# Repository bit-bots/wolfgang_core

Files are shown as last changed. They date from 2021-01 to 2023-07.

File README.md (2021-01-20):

# Wolfgang CORE
COntrolling and REgulating electronics for the Wolfgang robot platform

Documentation can be found [here](http://doku.bit-bots.de/meta/manual/hardware/electronics/wolfgang_core.html).

## Features
* Power over Ethernet (PoE) power source (for ethernet camera)
* Power regulation 5V ~5A (odroid/raspberry pi), 9V 1A (network switch)
* Power source selection (Battery or power supply)
* Switching of power to Motors (Manual and through software)
* RS485/TTL on 4 Buses with theoretically up to 12 MBaud (4MBaud tested since thats what our Dynamixel motors support)
* Voltage (including Cell voltage for LiPos) and Current monitoring
* 3 RGB LEDS!!!

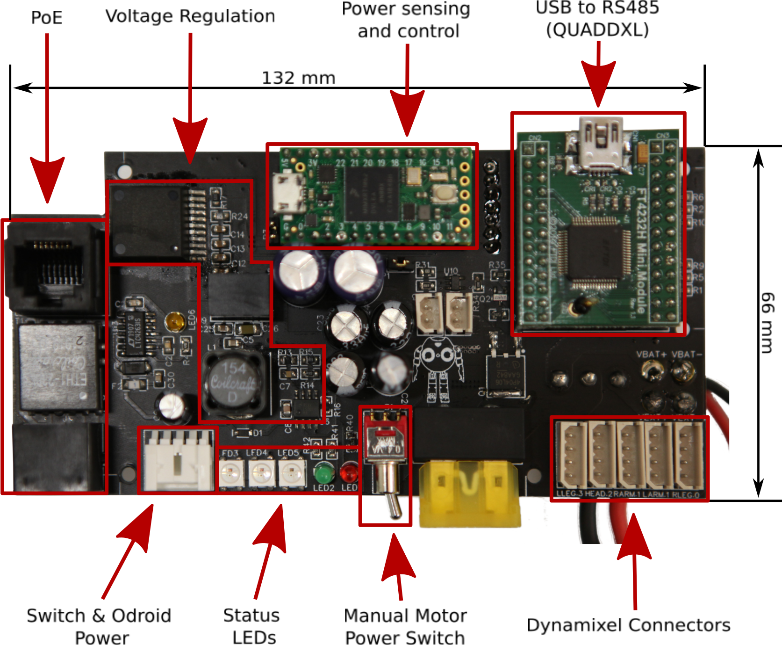
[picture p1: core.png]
Image of CORE


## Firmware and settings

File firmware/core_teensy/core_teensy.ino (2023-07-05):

#include <Dynamixel2Arduino.h>
#include <FastLED.h>
#include <EEPROM.h>

/*---------------------- LEDS ---------------------*/
#define LED_PIN 0
#define NUM_LEDS 3
CRGB leds[NUM_LEDS];


#define SWITCH_POWER 4
#define LED_DATA 0



#define VDXL_SENSE 23
#define VEXT_SENSE 22
#define VCC_SENSE 21
#define VBAT_SENSE_0 20
#define VBAT_SENSE_1 19
#define VBAT_SENSE_2 18
#define VBAT_SENSE_3 17
#define VBAT_SENSE_4 16
#define VBAT_SENSE_5 15
#define CURRENT_SENSE 14

#define SWITCH_POWER_SENSE 12

#define DXL_SERIAL   Serial2
#define DEBUG_SERIAL Serial
#define DEFAULT_BAUD 4 //2mbaud
#define DEFAULT_ID 42
const uint8_t DXL_DIR_PIN = 6; // DYNAMIXEL Shield DIR PIN

DYNAMIXEL::SerialPortHandler dxl_port(DXL_SERIAL, DXL_DIR_PIN);

const float DXL_PROTOCOL_VER_2_0 = 2.0;
const uint16_t DXL_MODEL_NUM = 0xabba; 
DYNAMIXEL::Slave dxl(dxl_port, DXL_MODEL_NUM);

#define ADDR_CONTROL_ITEM_BAUD 8

#define ADDR_CONTROL_ITEM_LED0_R 10
#define ADDR_CONTROL_ITEM_LED0_G 11
#define ADDR_CONTROL_ITEM_LED0_B 12
#define ADDR_CONTROL_ITEM_LED1_R 14
#define ADDR_CONTROL_ITEM_LED1_G 15
#define ADDR_CONTROL_ITEM_LED1_B 16
#define ADDR_CONTROL_ITEM_LED2_R 18
#define ADDR_CONTROL_ITEM_LED2_G 19
#define ADDR_CONTROL_ITEM_LED2_B 20


#define ADDR_CONTROL_ITEM_LED 22
#define ADDR_CONTROL_ITEM_POWER 23

#define ADDR_CONTROL_ITEM_VEXT 28
#define ADDR_CONTROL_ITEM_VCC 30
#define ADDR_CONTROL_ITEM_VDXL 32
#define ADDR_CONTROL_ITEM_CURRENT 34
#define ADDR_CONTROL_ITEM_POWERON 36
#define ADDR_CONTROL_ITEM_VBAT_0 38
#define ADDR_CONTROL_ITEM_VBAT_1 40
#define ADDR_CONTROL_ITEM_VBAT_2 42
#define ADDR_CONTROL_ITEM_VBAT_3 44
#define ADDR_CONTROL_ITEM_VBAT_4 46
#define ADDR_CONTROL_ITEM_VBAT_5 48

uint8_t control_item_led, control_item_power;
uint32_t control_item_led_rgb1, control_item_led_rgb2, control_item_led_rgb3;

uint16_t control_item_vbat[6], control_item_vext, control_item_vcc, control_item_vdxl, control_item_current, control_item_poweron;

bool manual_power_was_off = false;
uint8_t baud, id;
int sample = 0;
uint32_t dxl_to_real_baud(uint8_t baud)
{
  int real_baud = 57600;
  switch(baud)
  {
    case 0: real_baud = 9600; break;
    case 1: real_baud = 57600; break;
    case 2: real_baud = 115200; break;
    case 3: real_baud = 1000000; break;
    case 4: real_baud = 2000000; break;
    case 5: real_baud = 3000000; break;
    case 6: real_baud = 4000000; break;
    case 7: real_baud = 5000000; break;
  }
  return real_baud;
}

void setup() {
  //check initialzed
  if(EEPROM.read(2) == 'i') {
    EEPROM.write(0, 42);
    EEPROM.write(1, 6);
    EEPROM.write(2, 'i');
  }
  
  //blink to show on
  FastLED.addLeds<1, WS2812B, LED_PIN, GRB>(leds, NUM_LEDS);
  leds[0] = CRGB::Red;
  leds[1] = CRGB::Blue;
  leds[2] = CRGB::Green;
  FastLED.show();
  delay(200);
  leds[0] = CRGB::Black;
  leds[1] = CRGB::Black;
  leds[2] = CRGB::Black;
  FastLED.show();

  // initialize dxl
  id = EEPROM.read(0);
  baud = EEPROM.read(1);
  dxl_port.begin(dxl_to_real_baud(baud));
  dxl.setPortProtocolVersion(DXL_PROTOCOL_VER_2_0);
  dxl.setFirmwareVersion(1);
  dxl.setID(id);

  // Add control items.
  dxl.addControlItem(ADDR_CONTROL_ITEM_BAUD, baud);
  
  dxl.addControlItem(ADDR_CONTROL_ITEM_LED, control_item_led);
  dxl.addControlItem(ADDR_CONTROL_ITEM_POWER, control_item_power);
  dxl.addControlItem(ADDR_CONTROL_ITEM_LED0_R, leds[0].r);
  dxl.addControlItem(ADDR_CONTROL_ITEM_LED0_G, leds[0].g);
  dxl.addControlItem(ADDR_CONTROL_ITEM_LED0_B, leds[0].b);
  dxl.addControlItem(ADDR_CONTROL_ITEM_LED1_R, leds[1].r);
  dxl.addControlItem(ADDR_CONTROL_ITEM_LED1_G, leds[1].g);
  dxl.addControlItem(ADDR_CONTROL_ITEM_LED1_B, leds[1].b);
  dxl.addControlItem(ADDR_CONTROL_ITEM_LED2_R, leds[2].r);
  dxl.addControlItem(ADDR_CONTROL_ITEM_LED2_G, leds[2].g);
  dxl.addControlItem(ADDR_CONTROL_ITEM_LED2_B, leds[2].b);
  
  dxl.addControlItem(ADDR_CONTROL_ITEM_VBAT_0, control_item_vbat[0]);
  dxl.addControlItem(ADDR_CONTROL_ITEM_VBAT_1, control_item_vbat[1]);
  dxl.addControlItem(ADDR_CONTROL_ITEM_VBAT_2, control_item_vbat[2]);
  dxl.addControlItem(ADDR_CONTROL_ITEM_VBAT_3, control_item_vbat[3]);
  dxl.addControlItem(ADDR_CONTROL_ITEM_VBAT_4, control_item_vbat[4]);
  dxl.addControlItem(ADDR_CONTROL_ITEM_VBAT_5, control_item_vbat[5]);
  dxl.addControlItem(ADDR_CONTROL_ITEM_VEXT, control_item_vext);
  dxl.addControlItem(ADDR_CONTROL_ITEM_VCC, control_item_vcc);
  dxl.addControlItem(ADDR_CONTROL_ITEM_VDXL, control_item_vdxl);
  dxl.addControlItem(ADDR_CONTROL_ITEM_CURRENT, control_item_current);
  dxl.addControlItem(ADDR_CONTROL_ITEM_POWERON, control_item_poweron);

  // Add interrupt callback functions to process read/write packet.
  dxl.setWriteCallbackFunc(write_callback_func);
  
  pinMode(LED_BUILTIN, OUTPUT);
  pinMode(SWITCH_POWER, OUTPUT);
  pinMode(LED_DATA, OUTPUT);

  // set motor power off
  digitalWrite(SWITCH_POWER, HIGH);
  
  pinMode(SWITCH_POWER_SENSE, INPUT);
  pinMode(VCC_SENSE, INPUT);
  pinMode(VBAT_SENSE_0, INPUT);
  pinMode(VBAT_SENSE_1, INPUT);
  pinMode(VBAT_SENSE_2, INPUT);
  pinMode(VBAT_SENSE_3, INPUT);
  pinMode(VBAT_SENSE_4, INPUT);
  pinMode(VBAT_SENSE_5, INPUT);
  pinMode(VEXT_SENSE, INPUT);
  pinMode(VDXL_SENSE, INPUT);
  pinMode(CURRENT_SENSE, INPUT);
}

void loop() {
  
  // read power switch state
  control_item_poweron = digitalRead(SWITCH_POWER_SENSE);

  // check if manual power switch has been turned off and on again
  // if this is the case we want to turn on the whole power
  if(control_item_poweron && manual_power_was_off)
  {
    control_item_power = true;
    digitalWrite(SWITCH_POWER, HIGH);
  }
  manual_power_was_off = !control_item_poweron;

  // read voltages and current sensor
  control_item_vcc = analogRead(VCC_SENSE);
  /*control_item_vbat[0] = analogRead(VBAT_SENSE_0);
  control_item_vbat[1] = analogRead(VBAT_SENSE_1);
  control_item_vbat[2] = analogRead(VBAT_SENSE_2);
  control_item_vbat[3] = analogRead(VBAT_SENSE_3);
  control_item_vbat[4] = analogRead(VBAT_SENSE_4);
  control_item_vbat[5] = analogRead(VBAT_SENSE_5);*/
  control_item_vext = analogRead(VEXT_SENSE);
  control_item_vdxl = analogRead(VDXL_SENSE);
  control_item_current = analogRead(CURRENT_SENSE);

  // package processing
  dxl.processPacket();
  if(dxl.getID() != id) // since we cant add the id as a control item, we need to check if it has been updated manually
  {
    id = dxl.getID();
    EEPROM.write(0, id);
  }
}

void write_callback_func(uint16_t item_addr, uint8_t &dxl_err_code, void* arg)
{
  (void)dxl_err_code, (void)arg;

  if (item_addr == ADDR_CONTROL_ITEM_BAUD)
  {
    dxl_port.end();
    dxl_port.begin(dxl_to_real_baud(baud));
    EEPROM.write(1, baud);
  }else if(item_addr == ADDR_CONTROL_ITEM_LED){
    digitalWrite(LED_BUILTIN, control_item_led);
  }
  else if (item_addr == ADDR_CONTROL_ITEM_POWER){
    digitalWrite(SWITCH_POWER, control_item_power);
  }
  else if(item_addr >= ADDR_CONTROL_ITEM_LED0_R && item_addr <= ADDR_CONTROL_ITEM_LED2_B)
  {
    FastLED.show();
  }
}

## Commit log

2020-06-30 added schematic and pcb files
2020-08-13 adapt to teensy
2020-08-24 changed power behavior on startup
2020-10-27 firmware adjustment to version 1.0 of pcb
2020-10-27 preliminary version of automatic poweron/ untested
2021-01-15 design files v1
    [BOM.csv]
2023-07-05 remove unneccesarry reading of cell voltages
2023-11-20 initial with some rs485 stuff
    [usb_to_rs485.kicad_sch, wolfgang_core.kicad_pcb, wolfgang_core.kicad_sch]
2023-11-24 Initial version USB to RS485
    [connectors.kicad_sch, usb_to_rs485.kicad_sch, wolfgang_core.kicad_sch]
2023-11-27 Connectors copied
    [connectors.kicad_sch]
2023-12-11 Power largely done
    [connectors.kicad_sch, wolfgang_core.kicad_sch]
2023-12-12 more io stuff
    [wolfgang_core.kicad_sch]
2024-11-14 Further work on CORE REV2
    [connectors.kicad_sch, io.kicad_sch, poe.kicad_sch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]
2024-11-14 More work on CORE Rev2
    [power.kicad_sch]
2024-12-02 Further WIP on Power Rev 2.0
    [power.kicad_sch]
2024-12-02 Add ESD protection diode, add footprints
    [power.kicad_sch]
2025-01-06 Updated a Note
    [power.kicad_sch]
2025-01-16 Added 5V and 3.3V converters
    [power.kicad_sch, usb_to_rs485.kicad_sch]
2025-01-16 Add Power Switch, Sensing, Indicators
    [power.kicad_sch]
2025-01-20 Fixup Tranistors directions
    [power.kicad_sch]
2025-01-20 Edited notes
    [power.kicad_sch]
2025-01-27 Add starting point for 19V power supply
    [power.kicad_sch]
2025-01-30 Copy over PoE stuff
    [poe.kicad_sch]
2025-01-30 Add ESP32 in io
    [io.kicad_sch, power.kicad_sch]
2025-01-30 Rearrange pins
    [io.kicad_sch]
2025-02-27 Footprints hinzugefügt
    [connectors.kicad_sch, io.kicad_sch, poe.kicad_sch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]
2025-03-04 Assign almost all Footprints
    [connectors.kicad_sch, io.kicad_sch, poe.kicad_sch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]
2025-03-05 Fix Spox Stecker
    [connectors.kicad_sch]
